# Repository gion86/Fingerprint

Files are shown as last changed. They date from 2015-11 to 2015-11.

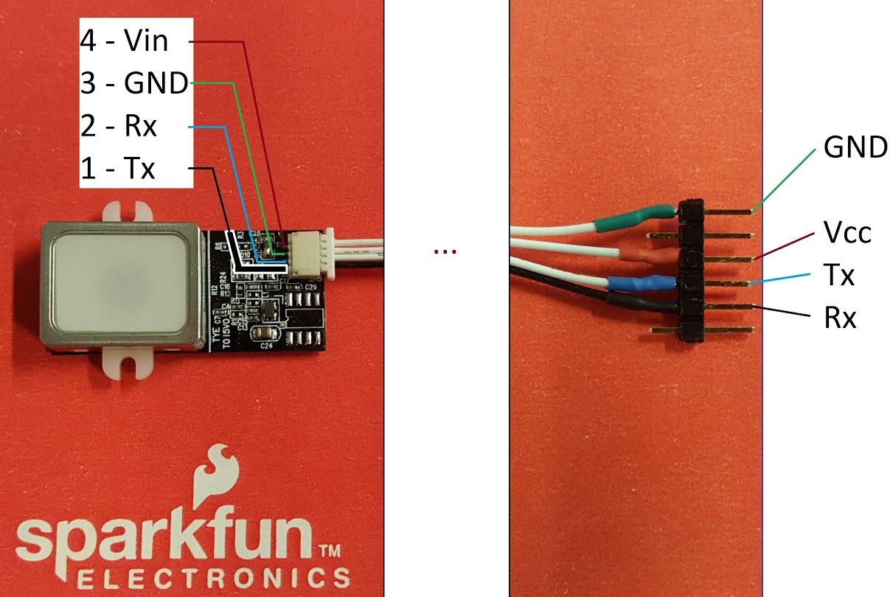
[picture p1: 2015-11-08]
Documentation/Datasheet/Fingerprint/FPS Connection.jpg

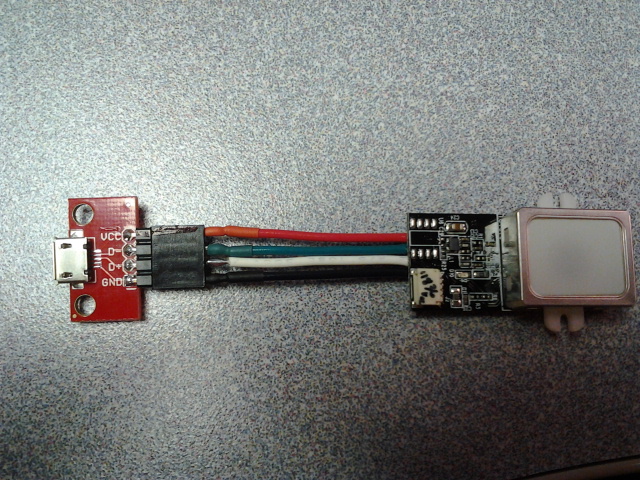
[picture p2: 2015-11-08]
Documentation/Datasheet/Fingerprint/GT511C1 Cable 3.jpg

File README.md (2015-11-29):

# FINGERPRINT Garage opener 
### Fingerprint sensor and relay output to open a garage door upon user authentication  
**version 0.9.6**

This project is made of a single main C++ file, which will be compiled for Atmel AVR 
architecture, and control fingerprint sensor (FPS_GT511C1R), with an Attiny84, to drive 
a relay contact. This will open/close my garage door!

The documentation folder contains:

* the bill of material;
* datasheet of used components;
* electrical drawings;
* library source code;
* wiring notes;
* code examples;

Some pictures can be found at https://goo.gl/photos/i5Vk5WsfXXiouzTf6

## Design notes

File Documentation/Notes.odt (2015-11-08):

Fingerprint Garage Opener notes

Ethernet cable connetions:

ETH cable | Function | FPS cable
G | RX | RX pin 1 (black)
WG | not used
BR | TX | RX pin 2 (white)
WBR | GND | GND pin 3
O | LED out
WO | VCC | VCC pin 4
BL | BTN in
WBL | not used

ATTiny84 programming connection, with USBASP programmer:

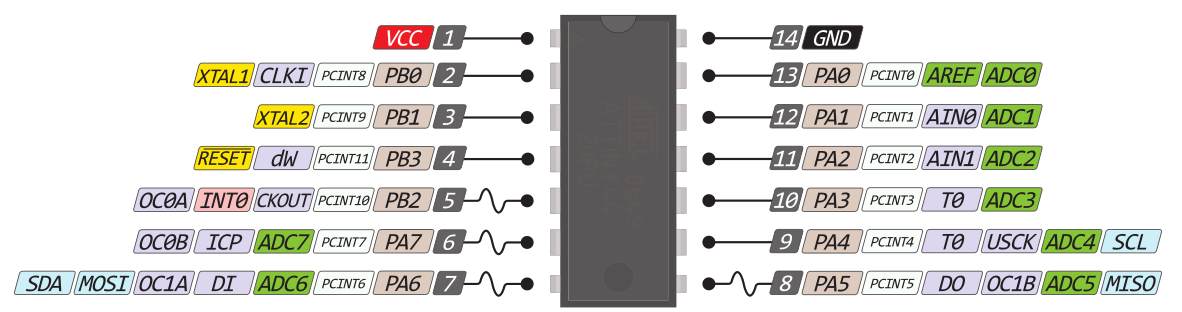
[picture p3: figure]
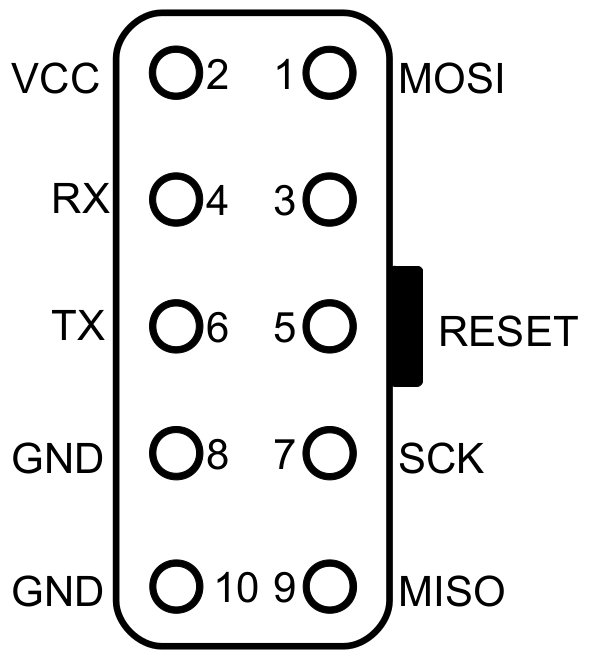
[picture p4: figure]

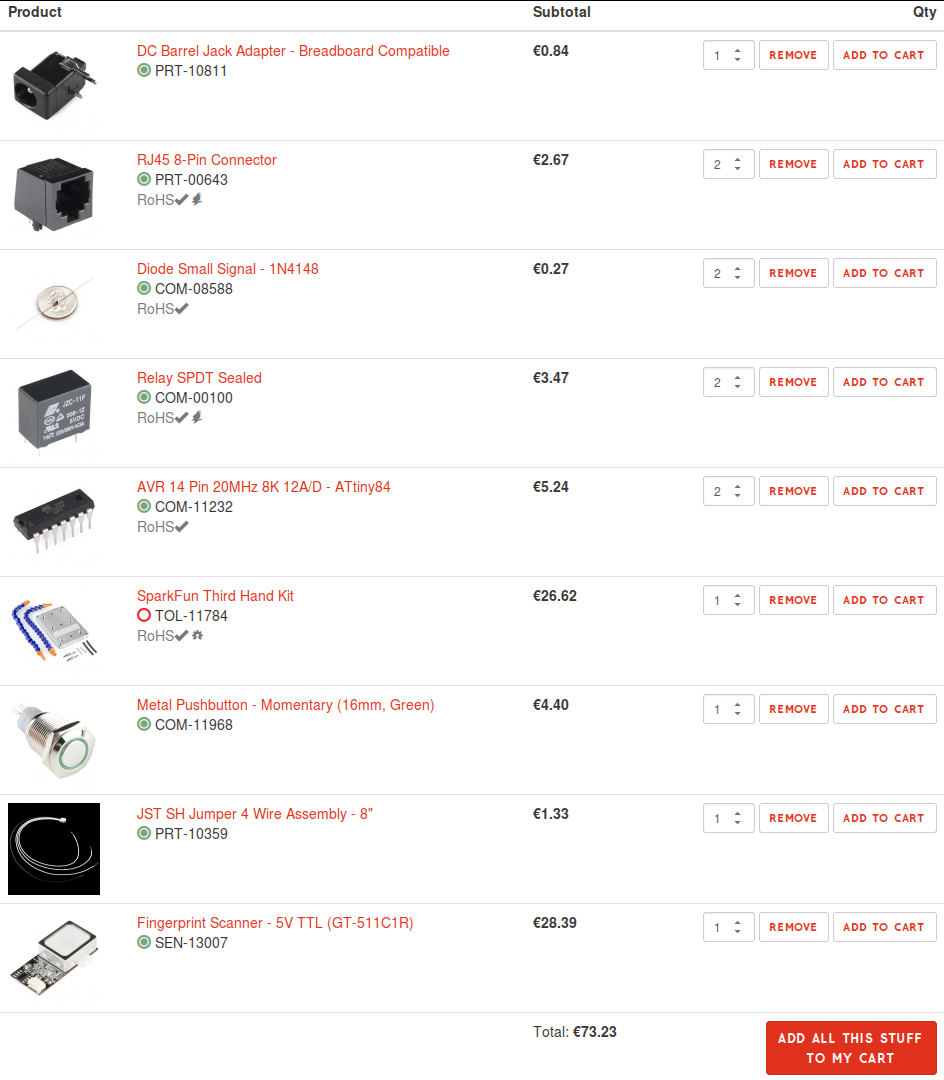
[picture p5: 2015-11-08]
Documentation/Sparkfun_garage.png

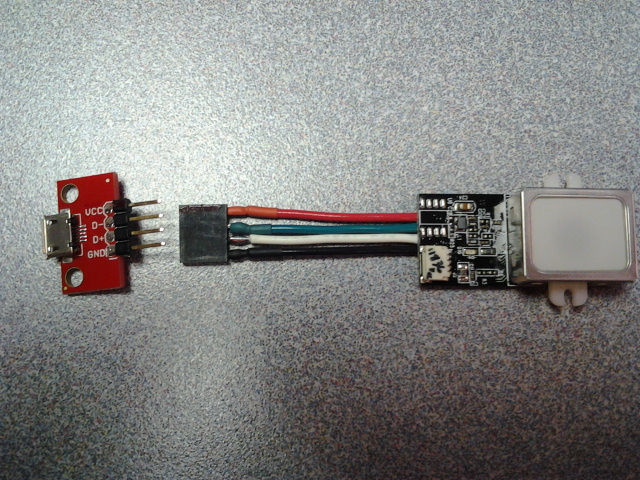
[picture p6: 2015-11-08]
Documentation/Datasheet/Fingerprint/GT511C1 Cable 1.jpg

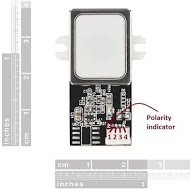
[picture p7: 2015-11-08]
Documentation/Datasheet/Fingerprint/GT-511C3.jpg

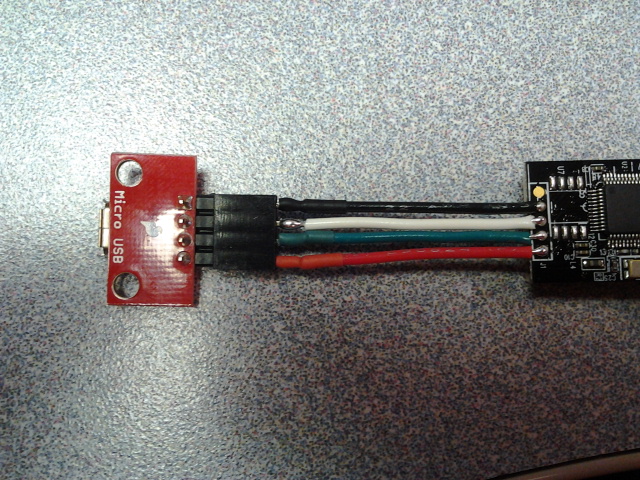
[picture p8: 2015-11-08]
Documentation/Datasheet/Fingerprint/GT511C1 Cable 2.jpg

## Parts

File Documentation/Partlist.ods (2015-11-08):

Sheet: BOM
GARAGE FINGERPRINT SCANNER BOARD
Part | Value | Device | Package | X | Where | Quantity | Price
C1 | 100uF | CAP_POLPTH2 | CPOL-RADIAL-10UF-25V | X
C2 | 0.1uF | C-US025-024X044 | C025-024X044 | X | Ebmstore | 10 | € 0,80
C3 | 2.2uF | CAP_POLPTH2 | CPOL-RADIAL-10UF-25V | X
D1 | 1N4148 | DIODE1N4148 | DIODE-1N4148 | X | Sparkfun | 2 | € 0,26
J1 |  | POWER_JACKPTH_BREAD | POWER_JACK_PTH_BREAD | X | Sparkfun | 1 | € 0,84
LED1 |  | LED3MM red | LED3MM | X
LED2 |  | LED3MM green | LED3MM | X
MCU1 | 2 | ATTINY84ATTINY84-20PU | DIL14 | X | Sparkfun | 2 | € 5,20
Q1 | 2N3904 | TRANSISTOR_NPNTO92 | TO-92 | X | Ebmstore | 10 | € 0,80
R1 | 1K | R-US_0207/10 | 0207/10 | X
R2 | 10K | R-US_0207/10 | 0207/10 | X
R3 | 200 | R-US_0207/10 | 0207/10 | X
R4 | 10K | R-US_0207/10 | 0207/10 | X
R5 | 200 | R-US_0207/10 | 0207/10 | X
R6 | 200 | R-US_0207/10 | 0207/10 | X
RELAY1 | FRS1B | FRS1B-S5 | RELAY | X
U$1 | RJ45-8PTH | RJ45-8PTH | RJ45-8 | X | Sparkfun | 2 | € 2,64
X1 | 1 | W237-102 | W237-102 | X | Ebmstore | 2 | € 0,80
 |  | SparkFun Third Hand Kit |  | X | Sparkfun | 1 | € 26,38
 |  | Metal Pushbutton (16mm, Green) |  | X | Sparkfun | 1 | € 4,36
 |  | JST SH Jumper 4 Wire Assembly |  | X | Sparkfun | 2 | € 2,64
 |  | Fingerprint Scanner - 5V TTL (GT-511C1R) |  | X | Sparkfun | 1 | € 28,14
 |  | Led verde alta luminosità 5 mm |  | X | Ebmstore | 10 | € 0,80
 |  | Portaled - 5mm - in acciaio cromato |  | X | Ebmstore | 10 | € 1,50
 |  | Zoccolo 14 pin per circuiti integrati DIL |  | X | Ebmstore | 10 | € 1,00
 |  | Basetta ramata 100x70 mono faccia |  | X | Ebmstore | 1 | € 0,80
 |  | Contenitore 90x56x23 mm – ABS nero |  | X | Ebmstore | 1 | € 1,20
 |  | Convertitore RS232 USB TTL con CP2102 |  | X | Ebmstore | 1 | € 3,50
 |  | Programmatore USBASP |  | X | Ebmstore | 1 | € 6,30
 |  | Alimentatore switching 5V 2A |  | X | Ebmstore | 1 | € 4,50
 |  | Penna circuiti stampati |  | X | Ebmstore | 1 | € 2,40
 |  | Basetta millefori 50x70 mm monofaccia in bachelite |  | X | Ebmstore | 1 | € 0,80
 |  | Supporto adesivo per basetta |  | X | Ebmstore | 10 | € 1,40
 |  | Tubi e varie |  | X | OBI | 1 | € 4,50
 |  | Cavo di rete |  | X |  | 1
 |  | Shipment |  |  | Ebmstore |  | € 5,33
 |  | Paypal fee |  |  | Ebmstore |  | € 0,82
 |  | IVA |  |  | Ebmstore |  | € 6,33
 |  | Shipment |  |  | Sparkfun |  | € 35,46
 |  | Import fee |  |  | Sparkfun |  | € 41,63
 |  |  |  |  |  |  | TOTAL
 |  |  |  |  |  |  | € 191,13

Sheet: Total cost
COST OF PROJECT
Component | Quantity | Price | Total Cost | Shipment Cost
Electronic
DIODE1N4148 | 1 | € 0,26 | € 0,26
POWER_JACKPTH_BREAD | 1 | € 0,84 | € 0,84
ATTINY84-20PU | 1 | € 2,60 | € 2,60
TRANSISTOR_NPNTO92 | 1 | € 0,08 | € 0,08
RJ45-8PTH | 1 | € 1,32 | € 1,32
Cable connector 5mm W237-102 | 1 | € 0,40 | € 0,40
JST SH Jumper 4 Wire Assembly | 1 | € 1,72 | € 1,72
Fingerprint Scanner - 5V TTL (GT-511C1R) | 1 | € 28,14 | € 28,14
Zoccolo 14 pin per circuiti integrati DIL | 1 | € 0,10 | € 0,10
Alimentatore switching 5V 2A | 1 | € 4,50 | € 4,50
Basetta millefori 50x70 mm monofaccia in bachelite | 1 | € 0,80 | € 0,80
Condensatori | 1 | € 0,08 | € 0,08
Construction
Contenitore 90x56x23 mm – ABS nero | 1 | € 1,20 | € 1,20
Metal Pushbutton (16mm, Green) | 1 | € 4,36 | € 4,36
Pipe and spare parts | 1 | € 10,00 | € 4,50
Network patch cable | 1 | € 0,00 | € 0,00
 |  |  | € 50,90 | € 0,00
 |  |  |  | TOTAL
 |  |  |  | € 50,90

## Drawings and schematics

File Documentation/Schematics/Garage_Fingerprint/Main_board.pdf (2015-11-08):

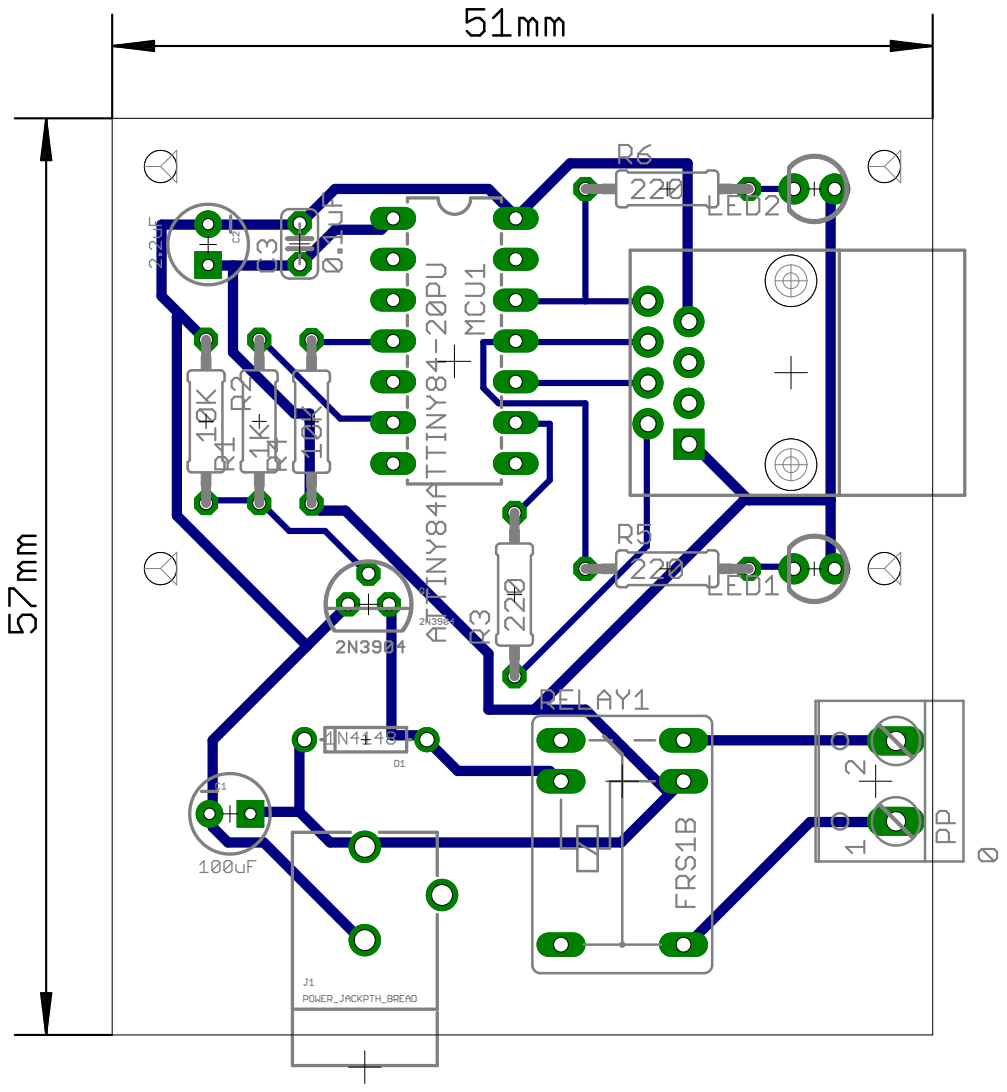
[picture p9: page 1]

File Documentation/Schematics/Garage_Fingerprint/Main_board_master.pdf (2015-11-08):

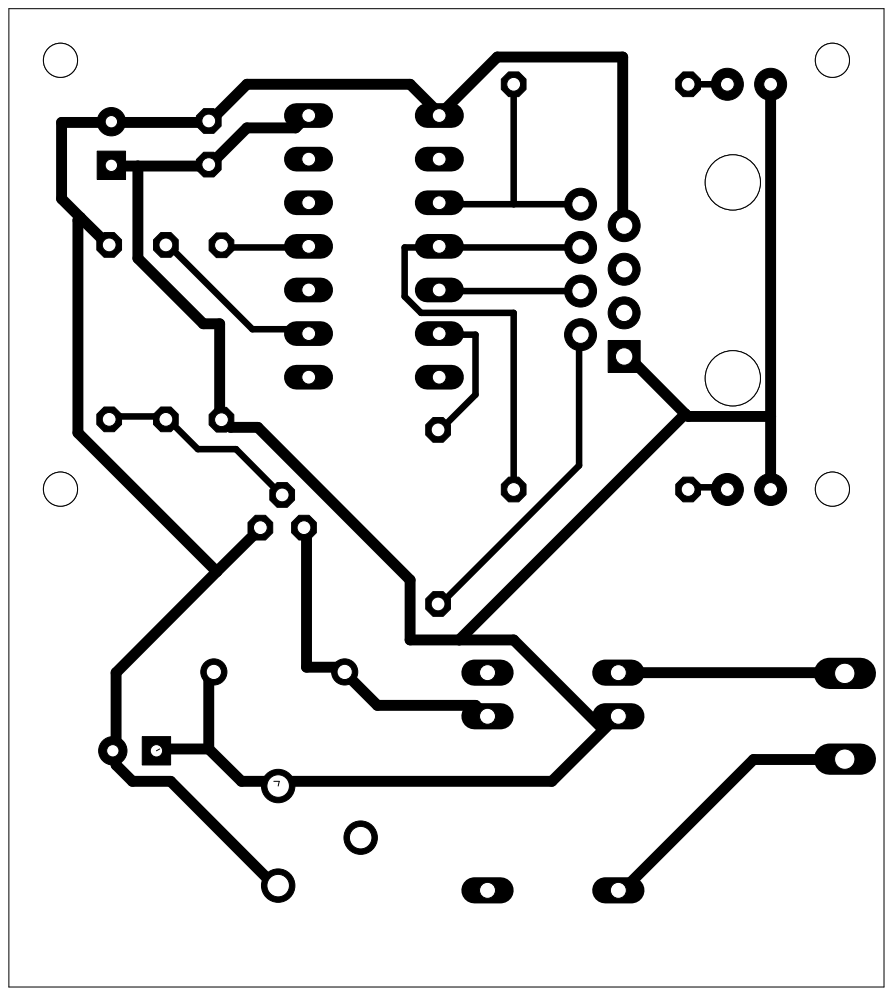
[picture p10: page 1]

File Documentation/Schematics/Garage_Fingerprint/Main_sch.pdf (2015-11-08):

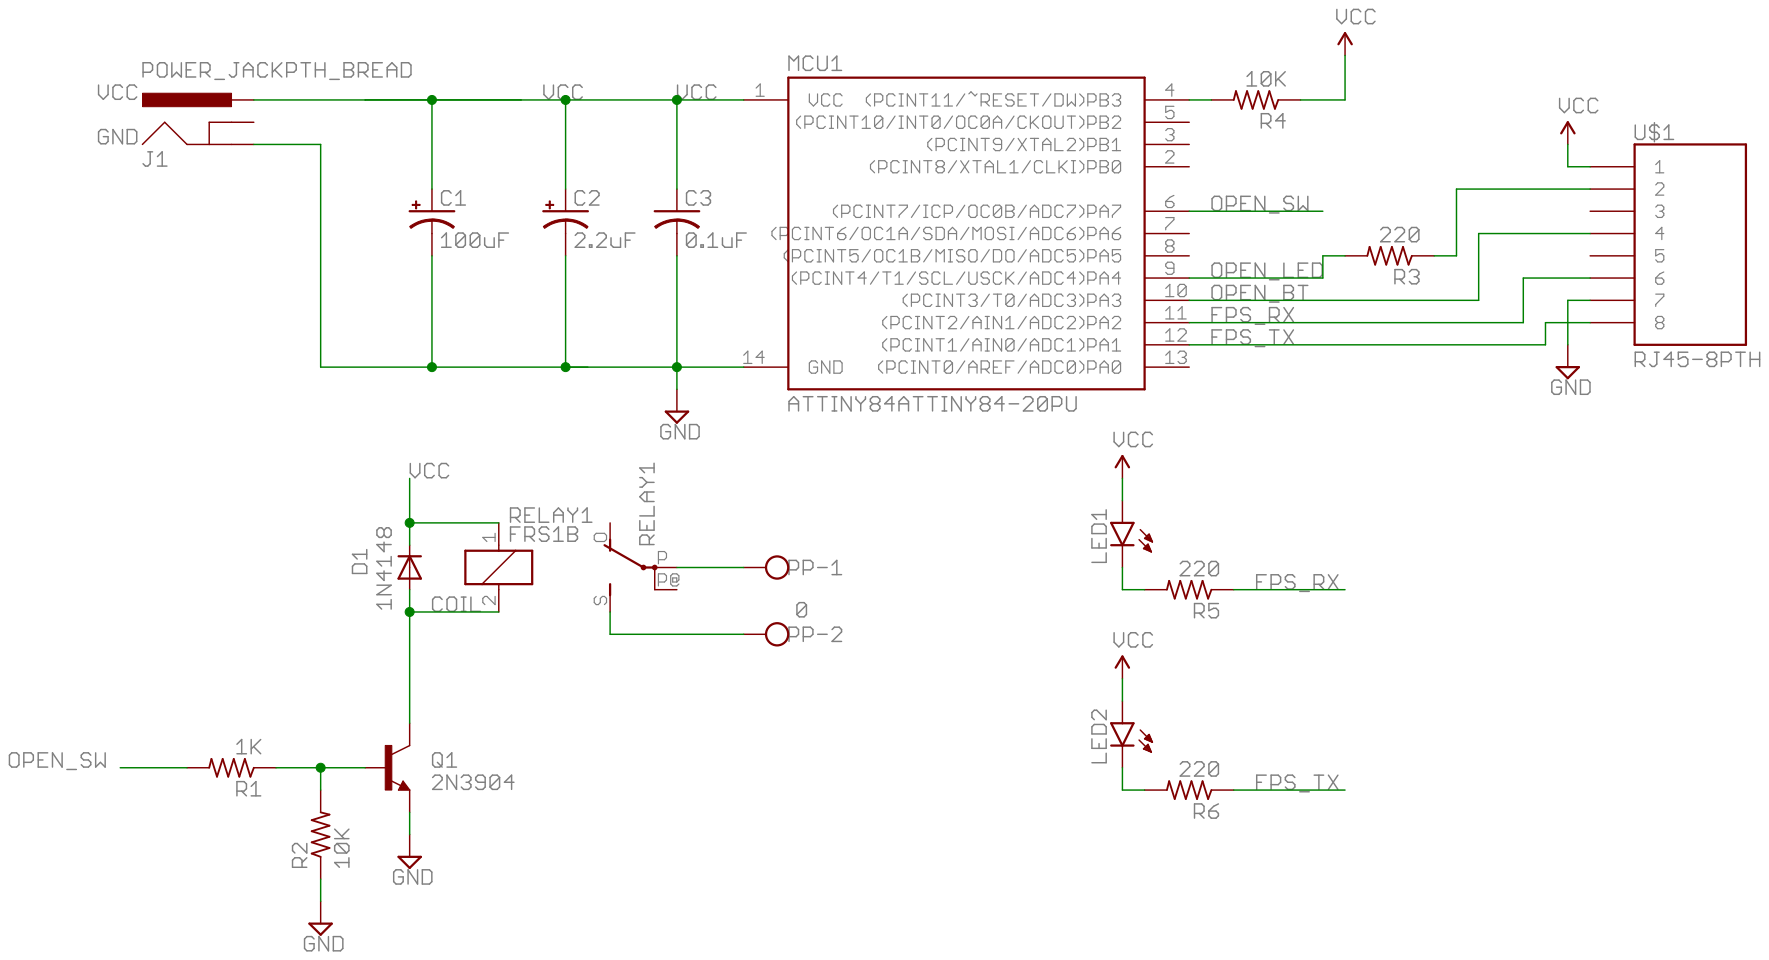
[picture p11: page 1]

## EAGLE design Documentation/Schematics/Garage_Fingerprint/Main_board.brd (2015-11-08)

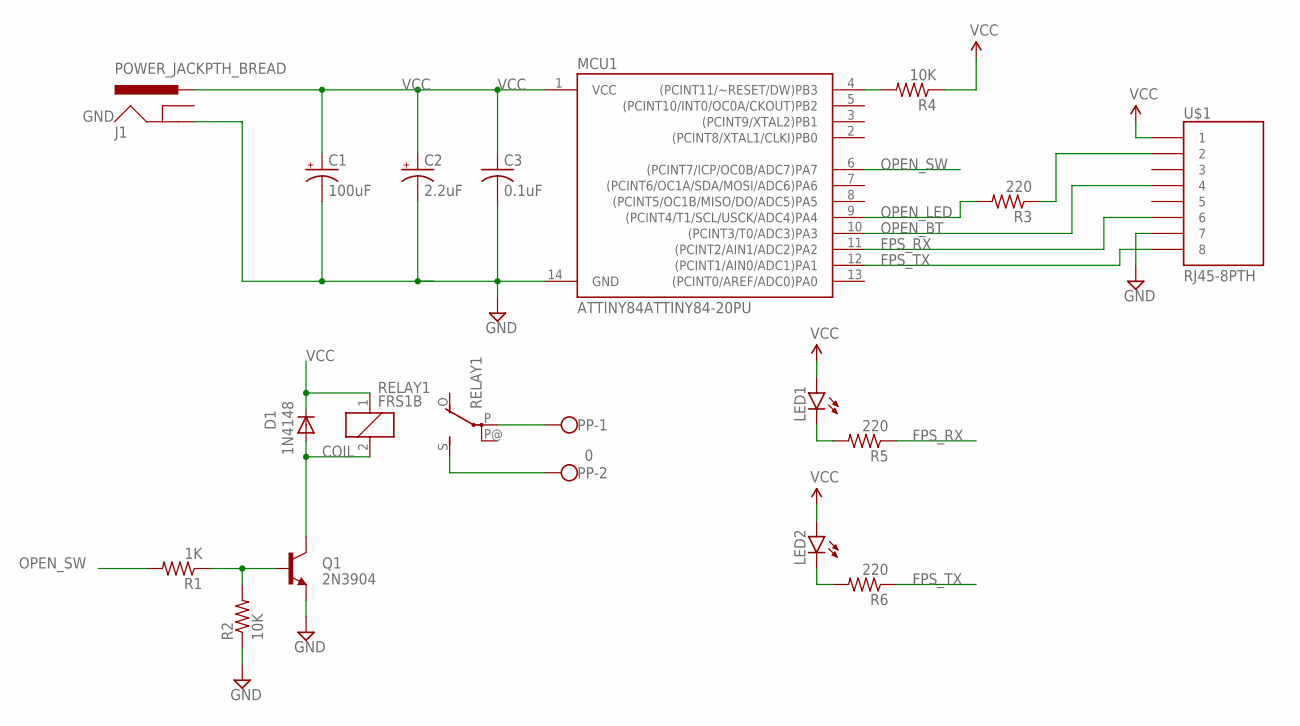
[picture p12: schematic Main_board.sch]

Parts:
C1: 100uF; CPOL-RADIAL-10UF-25V
C2: 2.2uF; CPOL-RADIAL-10UF-25V
C3: 0.1uF; C025-024X044
D1: 1N4148; DIODE-1N4148
J1: POWER_JACKPTH_BREAD; POWER_JACK_PTH_BREAD
LED1, LED2: LED3MM
MCU1: ATTINY84ATTINY84-20PU; DIL14
PP: 0; W237-102
Q1: 2N3904; TO-92
R1: 1K; 0207/10
R2, R4: 10K; 0207/10
R3, R5, R6: 220; 0207/10
RELAY1: FRS1B
U$1: RJ45-8PTH; RJ45-8

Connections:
COIL: D1.A, Q1.3 (C), RELAY1.2
FPS_RX: MCU1.11 ((PCINT2/AIN1/ADC2)PA2), R5.1, U$1.6
FPS_TX: MCU1.12 ((PCINT1/AIN0/ADC1)PA1), R6.1, U$1.8
GND: C1.2 (-), C2.2 (-), C3.2, J1.GND, MCU1.14 (GND), Q1.1 (E), R2.1, U$1.7
unnamed: Q1.2 (B), R1.1, R2.2
unnamed: PP.2, RELAY1.S
unnamed: PP.1, RELAY1.P
unnamed: LED2.K (C), R6.2
unnamed: MCU1.4 ((PCINT11/~RESET/DW)PB3), R4.2
unnamed: LED1.K (C), R5.2
unnamed: R3.1, U$1.2
OPEN_BT: MCU1.10 ((PCINT3/T0/ADC3)PA3), U$1.4
OPEN_LED: MCU1.9 ((PCINT4/T1/SCL/USCK/ADC4)PA4), R3.2
OPEN_SW: MCU1.6 ((PCINT7/ICP/OC0B/ADC7)PA7), R1.2
VCC: C1.1 (+), C2.1 (+), C3.1, D1.C, J1.PWR, LED1.A, LED2.A, MCU1.1 (VCC), R4.1, RELAY1.1, U$1.1

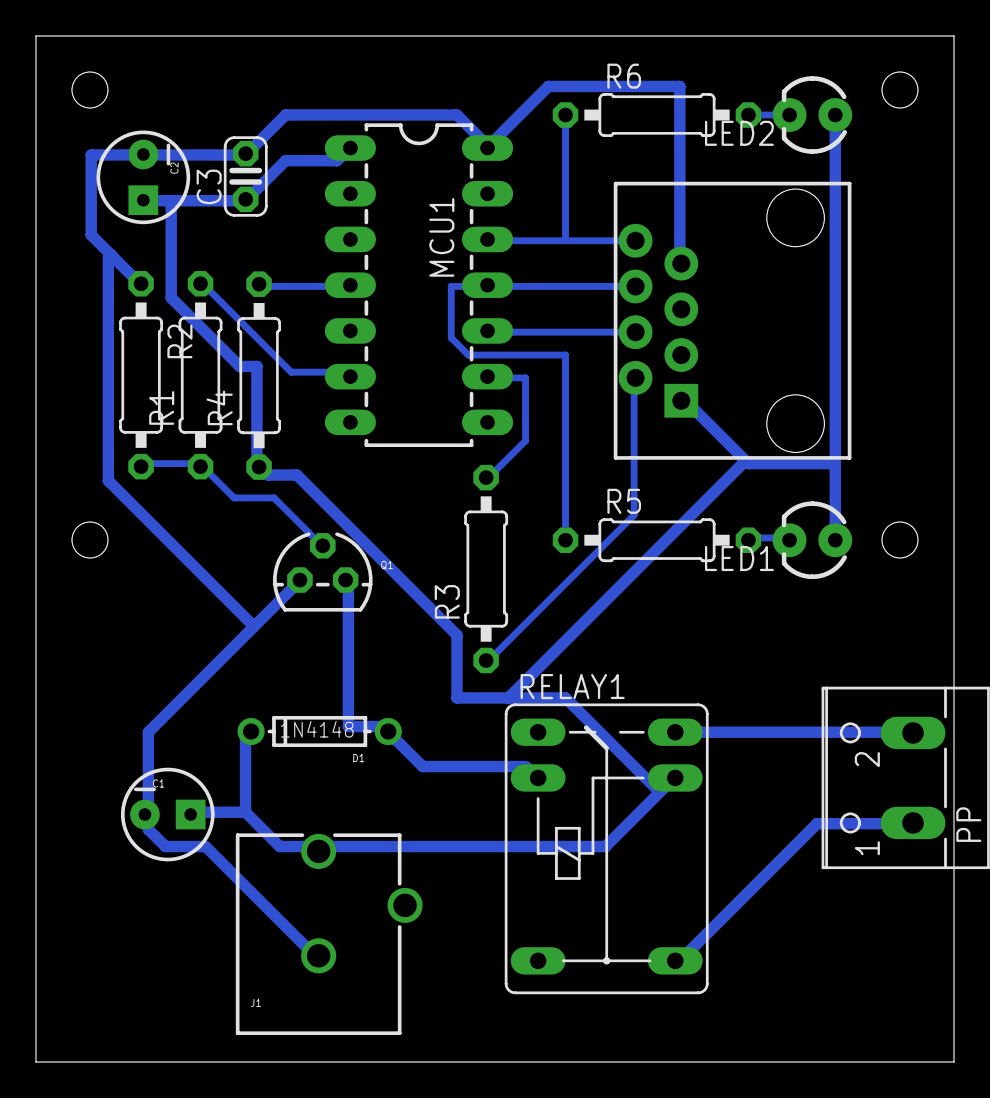
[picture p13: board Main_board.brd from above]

Board: 2 copper layers, 51.0 x 57.0 mm, 18 parts (0 on the bottom side), 15 nets.

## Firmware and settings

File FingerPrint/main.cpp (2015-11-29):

/*
 *  This file is part of FingerPrint garage opener application.
 *
 * Licensed under the Apache License, Version 2.0 (the "License");
 * you may not use this file except in compliance with the License.
 * You may obtain a copy of the License at
 *
 *    http://www.apache.org/licenses/LICENSE-2.0
 *
 * Unless required by applicable law or agreed to in writing, software
 * distributed under the License is distributed on an "AS IS" BASIS,
 * WITHOUT WARRANTIES OR CONDITIONS OF ANY KIND, either express or implied.
 * See the License for the specific language governing permissions and
 * limitations under the License.
 *
 */

/*
 * Built for Attiny84 8Mhz, using AVR USBasp programmer.
 * VERSION 0.9.6
 */

#include <Arduino.h>
#include <avr/sleep.h>

#include <FPS_GT511C1R.h>
#include <Bounce2.h>

#define SOFT_SERIAL_IN          8       // RX pin
#define SOFT_SERIAL_OUT         9       // TX pin
#define BTN_IN                  7       // Button in pin
#define BTN_LED                 6       // Button led out pin
#define RELAY_SW                3       // Relay out pin

#define LED_CLOCK               500     // [ms]
#define LED_FAST_CLOCK          250     // [ms]
#define RELAY_PULSE_DURATION    500     // [ms]
#define AUTH_REQ_TIMEOUT        15000   // [ms]
#define AUTH_TIMEOUT            35000   // [ms]
#define AUTH_CHECK_DELAY        100     // [ms]
#define DEBOUNCE_TIME           5       // [ms]

#define ID_NOT_VALID            200     // Returned ID when the finger is not recognized
#define MAX_AUTH_ID             20      // Maximum IDs supported by the sensor

#define STEP_SLEEP              0
#define STEP_WAIT               5
#define STEP_WAIT_AUTH          10
#define STEP_AUTH               15

// Fingerprint scanner sensor
FPS_GT511C1R fps(SOFT_SERIAL_IN, SOFT_SERIAL_OUT); // RX, TX

// Bounce2 instance
Bounce debouncer = Bounce();

unsigned long start = 0;
unsigned long startAuth = 0;
unsigned long clockStart = 0;
unsigned long clockDelay = 0;
unsigned long pulseOpen = 0;

// Starting step
unsigned short int step = STEP_SLEEP;
unsigned short int oldStep = STEP_SLEEP;

bool ledState = false;
bool autReq = false;
bool autGranted = false;
bool btnEdgePos = false;
int id = ID_NOT_VALID;

// Put the micro to sleep
void system_sleep() {
  set_sleep_mode(SLEEP_MODE_PWR_DOWN);
  sleep_enable();
  sleep_mode();

  // sleeping ...
  sleep_disable(); // wake up fully
}

// Reset internal variables
void reset() {
  ledState = false;
  autReq = false;
  autGranted = false;
  fps.SetLED(false);
  digitalWrite(BTN_LED, LOW);
  digitalWrite(RELAY_SW, LOW);
}

// ========================================================
// |                        SETUP                         |
// ========================================================

void setup() {

  pinMode(RELAY_SW, OUTPUT);
  pinMode(BTN_LED, OUTPUT);
  pinMode(BTN_IN, INPUT_PULLUP);
  pinMode(SOFT_SERIAL_IN, INPUT_PULLUP);
  pinMode(SOFT_SERIAL_OUT, OUTPUT);

  // After setting up the button, setup the Bounce instance
  debouncer.attach(BTN_IN);
  debouncer.interval(DEBOUNCE_TIME); // interval in ms

#ifdef DEBUG
  Serial.begin(9600);
//  fps.UseSerialDebug = true;
#endif
  fps.Open();
  reset();

  // Disable ADC to save power
  ADCSRA = 0;

  PCMSK0 |= (1<<PCINT3);    // pin change mask: listen to portA bit 3
  GIMSK  |= (1<<PCIE0);     // enable PCINT interrupt

} // End of setup


// ========================================================
// |                        LOOP                          |
// ========================================================

void loop() {

  // Update the Bounce instance
  debouncer.update();

  // Get the updated value :
  btnEdgePos = debouncer.rose();

  switch (step) {

    case STEP_SLEEP: // System sleep waiting for interrupt in PCINT3 (pin 7)
      system_sleep();
      step = STEP_WAIT;
      break;

    case STEP_WAIT: // Wait for button positive edge
      if (btnEdgePos) {
        autReq = true;
        fps.SetLED(true);

        start = millis();
        clockStart = millis();
        clockDelay = millis();

        step = STEP_WAIT_AUTH;
      }
      break;

    case STEP_WAIT_AUTH:  // Wait for finger on the sensor, or timeout
      if (millis() - clockStart >= LED_CLOCK) {
        clockStart = millis();
        ledState = !ledState;
        digitalWrite(BTN_LED, ledState);
      }

      // Delay some ms
      if (millis() - clockDelay >= AUTH_CHECK_DELAY) {
        clockDelay = millis();

        if (fps.IsPressFinger()) {
          ledState = true;
          digitalWrite(BTN_LED, ledState);

          if (fps.CaptureFinger(false)) {
            id = fps.Identify1_N();
            if (id <= MAX_AUTH_ID) {
              // Fingerprint identified: authorization granted
              autGranted = true;
              pulseOpen = millis();

              fps.SetLED(false);
              digitalWrite(RELAY_SW, HIGH);
              digitalWrite(BTN_LED, HIGH);

              startAuth = millis();
              step = STEP_AUTH;
            }
          }
        }
      }

      if (millis() - start >= AUTH_REQ_TIMEOUT && !autGranted) {
        reset();
        step = STEP_SLEEP;
      }
      break;

    case STEP_AUTH:
      if (millis() - startAuth >= AUTH_TIMEOUT) {
        reset();
        step = STEP_SLEEP;

      } else if (btnEdgePos) {
        pulseOpen = millis();
        digitalWrite(RELAY_SW, HIGH);
      }

      if (millis() - pulseOpen >= RELAY_PULSE_DURATION) {
        digitalWrite(RELAY_SW, LOW);
      }
      break;

    default:
      break;
  }

#ifdef DEBUG
  if (step != oldStep) {
    Serial.print("STEP = ");
    Serial.println(step);
    oldStep = step;
  }
#endif

} // End of loop

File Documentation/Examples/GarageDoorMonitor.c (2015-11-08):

    // Garage 2x Door Monitor and Fingerprint Opener
// Dave Astolfo www.plastibots.com
// Uses Blynk to process and display info over net from IOS/Android
// Uses Adafruit CC3000 breakout board for WiFi comms
// Uses Optiboot Nano bootloader (use Arduino v1.0.5 me)
// Uses watchdog timer due to issue with either Nano or CC3000 crashing - forces restart

// ********  Must select board:  [Optiboot] Arduino Duemilaove or Nano w/Atmega328 **********

#include <avr/wdt.h>         // required for watchdog timer
#include <SoftwareSerial.h>
#include "FPS_GT511C3.h" //the fps (fingerprint scanner) library
//#define BLYNK_PRINT Serial    // Comment this out to disable prints and save space

// These are the interrupt and control pins for 3000
#define ADAFRUIT_CC3000_IRQ   3
#define ADAFRUIT_CC3000_VBAT  5
#define ADAFRUIT_CC3000_CS    10

#include <SPI.h>
#include <Adafruit_CC3000.h>
#include <BlynkSimpleCC3000.h>


FPS_GT511C3 fps(2, 4); //RX, TX

const int door1ClosePin = 6;
const int door2ClosePin = 7;
const int door1LimitPin = A0;
const int door2LimitPin = A1;
const int OKLedPin = A5;
const int NotOKLedPin = A4;
const int doorStatLEDPin = 8; 
const int delayVal = 100; //in milliseconds
int i = 0;
int doorState = 0;  //value
int d1S, d2S, d1LimVal, d2LimVal;
boolean door_p1, door_p2, door_p3, door_p4;  //bits for door 1 pwd
unsigned long pwdEntryStartTime = 0;
long interval = 30000;  //30 second grace period to retain password to allow opening of doors.

// You should get Auth Token in the Blynk App. Go to the Project Settings (nut icon).
char auth[] = "authcodehere";


void setup()
{

  //Serial.begin(9600);  //for debugging - disable once live.
  
  
  pinMode(OKLedPin, OUTPUT);
  pinMode(NotOKLedPin, OUTPUT);  
  pinMode(doorStatLEDPin, OUTPUT);    
  pinMode(door1ClosePin, OUTPUT);        
  pinMode(door2ClosePin, OUTPUT);        
  pinMode(door1LimitPin, INPUT);    
  pinMode(door2LimitPin, INPUT);      

  
  fps.Open();
  fps.SetLED(true); //the fps LED
  fps.UseSerialDebug = false; //set to true for fps debugging through serial
  blink(OKLedPin, 1000, 1);
  Blynk.begin(auth, "SSID", "PASSCODE", WLAN_SEC_WPA2);
  blink(OKLedPin, 500, 3);
  wdt_enable(WDTO_8S);   //turns on watchdog timer with 8 second countdoor.  Sketch requires wtd_reset() to reset this, else a reboot is forced
}

void loop()
{

  wdt_reset();  //reset as it goes through each loop - necessary to ensure the watchdog timer does not reset the Duino when it's working fine.
  
  if (!cc3000.checkConnected())
  {
    wdt_reset(); //reset the watchdog timer in any normal op that may take time.
    Blynk.begin(auth, "SSID", "PASSCODE", WLAN_SEC_WPA2);
    blink(OKLedPin, 500, 3);
  }

  Blynk.run();                //start polling the system and reporting to the Blynk app.
  Blynk.virtualWrite(4, 1);   //sends a heartbeat to the Blynk app.
  
  // Only want to send / check door state values every 0.5s (500ms) seconds.  Based on the delay value set in the main loop
  // this takes care of it without using a timer - this also does not slow down the main loop
  i++;
  if (i == (1000 / delayVal) - 1)
  {
   Blynk.virtualWrite(4, 0); 
   checkDoorState();
   i = 0;
   blink(OKLedPin, 100, 1);  
  }
  //end timing a door state check
  
  
  //scan and identify the finger when one is put on it
  chkForFingerPrint();

  delay(delayVal);  
  
}



//************************************************************************************************************************************************
//future enhancement - allow for enrolling new fingerprints
void Enroll()
{
}


//************************************************************************************************************************************************
void chkForFingerPrint()
{
	if (fps.IsPressFinger())
	{
                wdt_reset();	//reset the watchdog timer for any normal op that may take time.	
                fps.CaptureFinger(false);
		int id = fps.Identify1_N();
		if (id < 200)
		{
			//Serial.print("Verified ID:");
			//Serial.println(id);
                        blink(OKLedPin, 100, 2);
                        Action(1);   //Open the Garage door
		}
		else
		{
			//Serial.println("Finger not found");
                        blink(NotOKLedPin, 100, 3);
		}
	}  
}

//************************************************************************************************************************************************
void blink(int whichLED, int dly, int numTimes)
{
  for (int i = 1; i<=numTimes; i++){  
    digitalWrite(whichLED, HIGH);
    delay(dly);
    digitalWrite(whichLED, LOW);
    delay(100);    
  }
}

//************************************************************************************************************************************************
void checkDoorState()
{
  //the master controller will send values to this analog pin when the doors are open. When closed, the value will be 0
  //will need to have 4 door state values.
  // door 1 = open, door 1 & 2 open, door 2 open.  all doors closed
  d1LimVal = analogRead(door1LimitPin);
  d2LimVal = analogRead(door2LimitPin);
  
  //Serial.print("Limit1Val:  ");
  //Serial.print(d1LimVal);
  //Serial.print("   Limit2Val:  ");  
  //Serial.println(d2LimVal);
    
    
  if ((d1LimVal >= 1000) && (d2LimVal >= 1000))  //both door limit switches are closed. 1023
  {
    d1S = 1;
    d2S = 1;
    blink(NotOKLedPin, 100, 1);
    msgOut(doorStatLEDPin, 1);
  }
  else if ((d1LimVal >= 1000) && (d2LimVal < 50))
  {
    d1S = 1;
    d2S = 0;
    blink(NotOKLedPin, 100, 1);
    msgOut(doorStatLEDPin, 1);   
  }
  else if ((d1LimVal < 50) && (d2LimVal >= 1000))
  {
    d1S = 0;
    d2S = 1;
    blink(NotOKLedPin, 100, 1);
    msgOut(doorStatLEDPin, 1);    
  }
  else
  {
    d1S = 0;
    d2S = 0;    
    msgOut(doorStatLEDPin, 0);
  }

  Blynk.virtualWrite(1, d1S);  //sends the state of Garage door 1 - if 1, then open
  Blynk.virtualWrite(3, d2S);  // sends the state of Garage door 2 - if 1, then open  
  
 
  //reset the timer values used for pwd entry
  if (millis() - pwdEntryStartTime > interval)
  {
    door_p1 = false, door_p2 = false, door_p3 = false, door_p4 = false;
    //reset the sliders in the Blynk app - do this after the interval time has elapsed.
	Blynk.virtualWrite(9, 0);  //pwd is no longer valid - update LED to OFF state
    Blynk.virtualWrite(5, 0);  //reset the pwd sliders to 0
    Blynk.virtualWrite(6, 0);  //reset the pwd sliders to 0  
    Blynk.virtualWrite(7, 0);  //reset the pwd sliders to 0
    Blynk.virtualWrite(8, 0);  //reset the pwd sliders to 0      
    pwdEntryStartTime = 0;
  }
  
  if (door_p1 && door_p2 && door_p3 && door_p4)
  {
    Blynk.virtualWrite(9, 1);  //pwd is correct - illuminate LED
  }
  else
  {
    Blynk.virtualWrite(9, 0);  //pwd is no longer correct - illuminate LED    
  }
  
    
}
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

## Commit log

2015-10-23 Fingerprint garage opener: first import of FPS_GT511C1R sensor library . Full credit to Josh Hawley for the library.
2015-10-23 Added a state to identify fingerprint. Added comments and safety checks.
2015-10-25 Commented out Serial print in SendCommand function: the print caused problems if UseSerialDebug = true!! Refactored projects configuration to compile for differente CPU targets.
2015-11-04 Added fps.IsPressFinger() on authentication step, to improve verification performance (stay active until the finger is released)
2015-11-07 Reverted back to one single step to authenticate, after some additional test the fingerprint sensor is working better and faster if using a delay of about 100ms between isPressFinger() calls. Changed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
    [main.cpp]
2015-11-08 Added Documentation folder with datasheets, schematic, bill of material..
    [Main_board.brd, Main_board.sch, Partlist.ods]
2015-11-22 Deleted fingerprint database and added to ignore

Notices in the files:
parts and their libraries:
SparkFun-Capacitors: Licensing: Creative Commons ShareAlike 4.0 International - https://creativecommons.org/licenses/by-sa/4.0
